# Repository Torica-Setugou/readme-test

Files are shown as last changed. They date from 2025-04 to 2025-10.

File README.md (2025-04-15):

# 接合班 引き継ぎ資料 班長業務編
## 目次
- スケジュール管理
- 予算
- 精度管理
- 班員管理
- 多方面との情報共有

## スケジュール管理
- 各班の年間スケジュールを立てるのは班長の最初の仕事である。これは、執行代が始まる前に済ませておくのが理想である。自分の代の設計思想,各班における新規性を取り入れる部分などが決定した瞬間から動き出すことが重要。代々、全体のスケジュールは執行代になって初めの役持ち会議ですり合わせるのが恒例になっているため、それまでに他班長,設計と新規タスクやある程度のスケジュール感を伝えあっておくとスムーズに執行代の製作を始められるからおすすめ。
- 接合班は、11月から本番機製作が始める。そのため、試作期間は8~10月の3か月のみである。その間で実現できる新規タスクなのかを判断してから、新規性を取り入れた年間予定を作ろう。じゃないと苦しむのはあなたたちです。この時、他班で取り入れる新規タスクが接合班に干渉する可能性まで考える必要があるので要注意。全部ひっくるめて製作可能なスケジュールを作るのだ！
- 年間予定で満足してはいけないよ。本番機製作からは特に、最低でも週ごとの予定はこまめに考えなければならない。例えば、
  - 11~12月(桁試験準備)のスケジュールは、9月末に週単位で作った。
    →桁がいつ届くのか、やすりに何日かかるのか…
  - 1~3月のスケジュールは桁試験直後の役持ち会議までに作った
    1月はテストでスケジュール考える暇ないよ
### スケジュール作成のコツ
- デッドラインを定める　ex)桁試験,全組,荷重試験…
- マージンを1週間位とる
- 作業のフローチャートを作り、各作業の所要日数から逆算していく
- 着手の日程を定める
### 進捗確認
以外に忘れがちなのは、実際に作業が始まってからの進捗確認。
今年は、インスタで流れてきた進捗管理スプシを見よう見まねで作ってみた。これがなかなか分かりやすく、視覚的に作業の遅延状況や順調さを認識できるのでおすすめ。
以下に、配布用のエクセルシートを置いておくので、使いたかったらご自由にどうぞ。



[配布用_タスク進捗カレンダー.xlsx](https://github.com/user-attachments/files/19748247/_.xlsx)

## 予算管理
- 各班の年間予算を決めるのは班長の業務である。予算を感がるにあたって、年間スケジュールを立てておく必要がある。そのうえで、前年の予算折衝スプシを分析して、必要なお金を算出する。(消耗品を忘れがちだから気を付けて)
- 25代の予算は105万。5万くらい余裕をもって申請しているから、足りないってならないように頑張っています。
- スケジュールと同様、現状確認も怠らないようにしています。こっちも、エクセルシートで作ったグラフに月末に使った金額を打ち込んで視覚的に残高を確認できるようにしました。これを作るには、月別の支出を立てないといけないので、なかなかな労力を必要とします。



## 精度管理
- 班に一人はOKかNOを判断できる人がいないとまずい。班長の役割じゃなくてもいいけど、副班長なり、何らかの役職を持たせておいた方が立ち回りやすくなるかな。というのは年末までの考え。最近は、役を持たなくても、各作業で、「この作業はこの人に聞けば大丈夫！」という人が1人ずついればいいかなと思えてきた。
- 実際、バンドソウを使う作業とか垂直に関してはすみかに任せっきりだし、すみかは役持ちじゃないけど不便を感じたことはない。逆に、役持ちになると視野が狭くなっちゃうから、役を持ってない人の方が全体を俯瞰できていたりする。こういう人は他の班にも存在していて、分かりやすいのはコクピの響互だね。この二人は特にその最たる例だと思う。本当に助かっている。役持ちじゃなく、精度管理できる様なひとに、会議内容を班長,副班長から共有すれば十分事足りる。

## 班員管理
- 自分の代と後輩について、何人いて、どれくらいのスキルをそれぞれが持っているのかを把握することが班員管理といえる。これを怠ると、一定の人にだけ作業が集中したり、本番機が始まって作業できる人がいないっていう事件が発生したりする。各代をしっかりと分析する必要がある。
- バンドソウやボール盤の危機管理も班員管理にはいるのかな。機械に慣れてない人に初めから細かい成形を任せたりすると、怪我のもとになる。実際にヒヤリハットでも経験してれば分かりやすいんだろうけど、意外に細かい危険もあるよというのは伝えておこう。

## 多方面との情報共有
- これ、大事。接合班は特に、他班との連携が多いから尚更。T字-コクピ班、かんざし-翼班、垂直リンク機構-電装班といった具合に、接合が終わらないと他班の製作が着手できないっていうことが起こりうる。そうならないために、どの作業がいつ頃終わりそうか、干渉する部分がないかを話し合うことが必要である。
- また、設計との情報共有も重要で、お互いにやりたいこと、できること、できないことをすり合わせておくことが重要。運営については、借用が発生するときに連携が必要になるため、ここの情報交換も大切。

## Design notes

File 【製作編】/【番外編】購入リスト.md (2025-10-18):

# モノタロウ購入リスト
- ここに載っていなければ、"ロイヤルホームセンター南千住"か"Amazon"で探せば見つかる




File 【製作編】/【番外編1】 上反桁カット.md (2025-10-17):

# 上反桁カット

## 24代(Ray)の上反角
- 偏心かんざし(中子)を使用
- 端側の桁径を落として、根側の桁に斜めに差し込むタイプ
- 中子はDMM.makeで発注(両翼でたしか14万)
- エポパテ(24hエポ+エロジール増粘剤)で接着したが、ねじり担保が不十分だったため、偏心フランジを作成した




## 25代(竜海)の上反角
- いわゆる桁焼きを導入
- 上反角部で桁径を落とさないでよいため、設計的な剛性UP
- Rayでは既製品同士の接着だけでよかったが、竜海では桁カットが必要となった
- ちなみに、桁発注先のスリーホープでも斜めにカットはしてもらえるようだが、1カット8万と言われた
- 竜海は2段上反だったため、カット代だけで64万⇒部内で加工することでコストカット
- このカットがなかなか緊張感のいるもので、ちょっとでも左右翼で桁長さが変わるとたわみが変わる
- "ミスの許されない","高精度"の斜めカットを8本もやらなきゃいけないため、終始ガン萎えしながら切ってた

S__62791684

## 上反桁カットの手順
① まず、2分割する
- ここの精度はいらない
- 気楽に行こう

② 必ず、きれいな縁の方から長さを測って、"上反角部(斜め)"⇒"端部(まっすぐ)"の順でマスターを貼る
- まず、きれいな縁から図った上反角部までの長さを測定してマスターを貼る
- その長さから使用長さを差し引いた分を測定してマスターを貼る
- マスターは、マステで何か所か仮止めした後に、クリアテープで固定すると切りやすかった

③ "上反角部(斜め)"⇒"端部(まっすぐ)"の順で桁をカットする
- 上反角部はミスってもきれいな縁側にマスターをずらせばやり直せる
- 端部はミス許されないし、ミスると設計値に影響を与えるから最重要項目

スクリーンショット 2025-10-17 231427

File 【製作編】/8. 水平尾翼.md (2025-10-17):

# 8. 水平尾翼
7F49A58A-82DC-40C8-B008-F76D33B60D1D

## 8.1. 機構(Ray)
- 桁にエビネットを打ち込んで迎角調整版の回転中心とした。
クナイは水平桁スパンの中心ではなく、テール桁に添うようにずらして接着した。


## 8.2. 接着方法(Ray)
①レーザーを駆使して、垂直桁に対して水平桁が直交するように仮止めする。


②水平の中心のリブの罫書き線に合わせて迎角が0°になるように部品を本接着する。
- 24代のゴリゴリの人たちと一緒に数人で半日かけて頑張った。

## 8.3. 機構(竜海)
福田のなんちゃって機構学を基に機構は考えました。
Ｍ科2年後期で機構学を学べるそうなので、ちゃんと勉強したらもっといいものができるかもですね。


E331C7FF-E697-48C7-85B9-4641E61322DE

部品は、以下の5つ
- 水平マウント
- クナイ
- ジョイント部品
 - フランジ(耳)
 - 迎角調整マウント

エポ抜きで合計200gくらい
62B900CD-F821-49E6-81BC-57193AB1ED82

## 8.4. 水平マウントの作り方
①MDFで治具を作る。
- 桁を治具にすることで精度を担保
- 真空引きするときに歪まないよう、中にカネライトを詰める。
- ボルト穴部分にM6スペーサーを埋め込む
- 固定はクリテのみにして、脱型をラクに
36C7E25B-A5B1-4F54-9043-97BB3D0BC56D

②積層する
- 積層構成は「0-0-45-0-0-バルサ-0-0-45-0-0」
- 2mmバルサを含めて11層

③成形
- 干渉しないように製図する
- スペーサーを入れ込むこと検討したが、公差が大きいという理由でボツにした

## 8.5. 接着方法(竜海)
- 水平の接着における前提条件として以下の3つの要素があることを理解しておく。
- これらがドンピシャになるように接着することが重要
- 「ヨー」「ロール」「ピッチ(迎角)」


⓪垂直の内棒接着とテールの鬼目ナット埋め込みまで完成

①水平桁にクナイを接着

64F91B38-F99B-403E-9861-0FF9F3199E24

②マウントにM6長ボルトを通し、垂直内棒に対してロールを合わせる。
720C8004-FAAB-4B62-AF3D-765164BA68EE

③テールにマウントを接着
 - マステで目張りしてから
 - 接着は30エポ
 
④水平桁にフランジを通し、クナイ,フランジ,水平マウントにM6長ボルトを通す。

⑤水平桁のヨー,ロールを確認し、フランジの接着位置を決定
B31F3569-46E0-4050-AAA3-0F05BB76B13F
E951E330-76D0-4908-BC5C-53F4EC77F39A

⑥水平桁にフランジを接着
 - アルテコで仮止め
 - 本接着は30エポ

⑦クナイのフランジ部分をリューターで切り落とす

⑥水平翼製作(翼班)

⑦クナイ,ジョイント部品,迎角調整マウントを0degの穴で締結

⑧水平翼の迎角を0degに合わせて迎角調整マウントを接着

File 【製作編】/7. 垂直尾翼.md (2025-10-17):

# 7. 垂直
7F49A58A-82DC-40C8-B008-F76D33B60D1D
- 鳥科では代々、サーボを用いた平行リンク機構を用いている。
- Rayでは、内棒(CFRP)と垂直桁の間にベアリング(ころ軸受け)を入れてラダー操作の平滑化を図った
- 竜海では、ベアリングの代わりにPOM(ポリアセタール樹脂)の円筒を入れた軽量化,平滑化を図った

## 7.1. 接着方法(Ray)
①テールにマスターに沿ってリューターで穴を空ける

②テール桁内部に30エポを塗る

③中子を内棒が刺さる位置まで滑り込ませる

④内棒を刺して、レーザー出し



## 7.2. 機構(竜海)
- 機構は平行リンク機構を採用(去年までを踏襲)
- 今年はサーボと垂直桁間距離を抑えて小型,軽量化を図った
- また、25代ではロックナットやねじロック剤を導入
  - ニュートラルが安定しない欠点をカバーするため
  - 飛行時のゆるみを抑えるため
- 秋葉原の「スーパーラジコン」で購入
2004D83C-8483-4797-ADE8-88B31B46DB51

## 7.3. 中子(竜海)
- 垂直の中子設計は、班員(同期&後輩)に一任していた。(とはいえ、一緒に考えていたため全部理解してるのでご安心を)
- 必要な条件は、"グラスホフの定理"のみだが、平行リンク機構ではほぼ考えなくてよい
- 今年のテーマは"小型軽量化","サーボ取り外し可能"

### 小型軽量化
- 垂直-サーボ間距離を短縮
- ロッド部品をM6⇒M4に変更
- 補強材として適宜カネライトを使用

### サーボと取り外し可能
- サーボの4隅にあるタッピング用の穴を拡張して、M2の長ねじを使用した。
- 中子には高ナットを埋め込んだ



## 7.4. 接着方法(竜海)
### 中子接着

① 中子に電装ケーブルを通す

② T字と同様の方法で内棒の位置を決定,接着

③ 中子に桁内側に添うようなカネライト治具を30エポで接着
 - 接着面積は少ないが、十分の強度を担保
 - 何より桁に腕を突っ込まない分接着がラク

### フランジ接着

平行リンク機構では、サーボホーンとフランジで以下の条件を揃える必要がある
- 桁中心からボルトまでの距離
- 桁上面からの高さ

→MDFの治具を汲んで以上のパラメーターを揃えた。
S__53436423

### 実際に動く様子

https://github.com/user-attachments/assets/fe7d19f1-72d2-4a0c-af30-e99af3f56bf8

## 7.5. 本番フライトでの様子
### 垂直尾翼取り付けの流れ
① 夜間保持終了時刻にテールにサーボを搭載

② 機体運搬直前に垂直フランジにロッドエンドを締結(ロックナットで接合)

③ 機体運搬途中でサーボの通電チェック

④ ニュートラル合わせ(1回目):サーボホーンとテールの罫書きの垂直を差金で確認

⑤ ねじロック剤でサーボホーンを本締結

⑥ 桟橋で垂直桁接合(ロックナットで接合) ←当初の予定ではプラホ上の予定だったが読売から指示がでた

⑦ サーボ通電チェック：テールから基盤までのコネクタが外れていた

⑧ ニュートラル合わせ(1回目)：後縁を翼副班長とダブルチェック

⑨ ドーサルフィン固定

### プラホ上での挙動

① フライト直前に左旋回方向に少々ずれているのを後方指揮が確認
S__167411735

② 手で動かすと、サーボのガタ(しょうがない可動域)の中でニュートラルに直った
S__167411737

③ 走り出しの衝撃でまた左旋回方向にズレる
S__167411739

- どうやら、ラダーが定常状態に戻っていなかったらしい

- ただ、サーボ自体に存在するガタも存在するため、さらに高みを目指すなら工夫が必要
- サーボの軸とサーボホーンの固定に使われる円盤は歯車状の構造のかみ合わせであり、既製品である以上多少のゆとりをもって作られている
- このガタを考慮してガタの中心またはあえてガタの端がニュートラルになるように設定するのか、ガタがないような構造を考えるのか、、
- 25代ではしょうがないと割り切ったが、こだわる労力があるならぜひ改善してほしい

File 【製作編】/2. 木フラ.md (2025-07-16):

# 2. 木フラ
S__51159047

## 2.1. 作り方とポイント
①ホワイトウッド板材に分割方向と垂直方向に中心線を引き、その線に合わせて穴あけマスターを張る
- ０端,1根：38×184×360
- その他：38×140×360

②センターポンチで円の中心にしるしをつける

③“美女と野獣(自在錐)”で円形を切りぬく
- 大きいクランプ2つでガッチリ固定する
- 刃の固定は複数人で確認する

④Φ6mmの短いドリルで4つのボルト穴をあける

⑤Φ6mmの長いドリルで2つの側面ボルト穴を開ける
- 万力を小さいクランプで固定する
- 木材が台座にほぼ垂直に立っているか確認する

⑥バンドソーで縦長に半分に切る

[木フラ_ボール盤_工程別安全チェックリスト.pdf](https://github.com/user-attachments/files/19749276/_._.pdf)

## 2.2. 接着方法
① 木フラ接着部に養生テープを2周巻く。その隣に1週巻く。



② 分割した木フラを桁にぴったりと接するように桁接着面をやする
- ここが踏ん張りどころ

③ 木フラの中心線(下図緑線)を桁の罫書き線(下図赤線)に合わせて30エポで接着する
- 木フラの穴あけ精度が重要



④エポが硬化したら桁接合をしてドリルでボルト穴を拡張する
- ボルトがガタつかない程度まで

## 2.3. ドリルの先端形状について
- ドリルの先端形状には、"先三角"と"先ねじ"の2種類がある。
- これらの違いによって使用用途別で向き,不向きがあるので注意が必要。

### ①先三角
- 先端が三角形になっている一般的なタイプ
- このタイプはボール盤やインパクト等、幅広く用いることができる
- 使用時には、穴を空けたい材に対して垂直に力を加え続ける必要がある
- 逆に、上から力を加えなけらば、穴は進まない

### ②先ねじ
- 先端がねじのようになっている特殊タイプ
- このタイプは、インパクトには向いているが、ボール盤には不向きである
- インパクトでの使用時
  - 先端のねじ形状により、始めのきっかけの力さえ加えれば、自身の推進力により穴を掘り進めてくれる。
  - 先三角のように力を加え続けなくても穴が開くため便利
- ボール盤での使用時
  - 始めのきっかけを与えると、ねじ形状の推進力で材が持ち上げられる。
  - クランプが不十分であったり、1点指示であったりすると材が浮き上がり、ボール盤の回転に追従して暴れてしまうため危険。
  - ただし、しっかりと2点止めでクランプ固定していれば、勝手にドリルが下に掘り進められていくだけで、あまり危険ではない。
  - 木フラで使う"美女と野獣"のうち、去年新たに買ったものは先ねじであるため、注意してください。

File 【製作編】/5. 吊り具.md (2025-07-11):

# 5. 吊り具
6A44E5E5-74C8-4AA1-B082-F8FC85E9DCC1

- 吊り具は、コクピフレームとT字をつなぐ部品です。
- でも、実はあんまり強度がしっかりしてなくても大丈夫なんです。
- なぜなら、フレームとT字の締結強度を受け持っているのはホースバンドだから。
- このことに気づいて、24代の本番機以降は積層枚数が11枚→7枚に減らしました。
- 他チーム(MaPPLとか)だと吊り具の上側がただのゴム板でホースバンドの間に緩衝材として挟んでるだけだったりする。
- ただし、吊り具の下側はフレームの高さを決めるために必要なので、精度とある程度の強度が欲しいところ。
- どっかの代で、やっぱり怖くね？ってなったら11枚に戻してください。
- ちなみに、積層構成は0°だけです。

## 5.1. 作り方とポイント(澪以前)
①下図赤線部の治具を作り、積層する。


C63A4170-E80B-44E7-A143-39A828A9E806

②成形する。

③下図青線部をスタイロで切り出す。



④アルミ角柱と積層物をブラインドリベットで締結する。

⑤積層物に③のスタイロ部品を接着する。

## 5.2. 作り方とポイント(Ray,竜海)
- 一言でいえば、新方式では、桁を治具として使った。
- なぜそうしたかというと、旧方式では赤線部治具の誤差と緩衝材部品の誤差が相まって積層物にスタイロがハマりにくかったから。
- 緩衝材部品はRayまではスタイロ,竜海ではカネライト
  - 特に理由はない

①下図のようなコの字の治具を作る。



②桁を①の治具に罫書き線に合わせて乗せ、反対側から青線部の緩衝材部品を乗せる。
S__51159048

③緩衝材部品,コの字治具,桁をまとめてクリアテープで保護し、積層する。



④成形し、ブラインドリベットでアルミ角柱と締結する。

⑤積層に使った緩衝材部品を接着する。
S__51257350

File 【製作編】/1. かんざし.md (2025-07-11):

# 1. かんざし
9D03ED82-0A8D-49DA-AA37-B976888E7A47

## 1.0. 概要
- 径差を埋める役割を担っている
  - 端側に行くにつれ、桁の直径が段階的に小さくなる
  - 太い桁に細い桁を挿して接合する

- 鳥科では、桧角材を用いた「木かんざし」を採用
  - プロペラ機のチームでは、ウレタンを充填した表面をカーボンで積層した「ウレタンかんざし」が多い
  - 径差が大きい部分では有効的だが、鳥科の径差ではあまり効果が感じられず、導入しなかった

- 24代機では、上反角を「偏心かんざし(上反角中子)」を外注しで作っていた。
  - 逆に言うと、かんざしが新円に作れていなければ思わぬ上反ができてしまう。

## 1.1. 作り方とポイント
①差し込み長さを養生テープでマークする
- ここを甘く見ていると、たわみの左右差が発生する

② 角材を均等に接着する
- 表面にエポが付着しないように頑張ると後でラク

③ やする
- 偏心していないかのチェックはこまめにやろう

④ GFを巻く
- 積層後GF厚みは1層:0.3mm,2層:0.4mm
- おそらくそれ以上は+1層毎に+0.1mm)

⑤ スズランで均等に圧着する
- しわが無いように注意する
- シュリンクテープでもいいかもね

⑥ 24h待つ

⑦ やする
- 微小なガラス粉末が舞うため、マスクをすることを推奨する

⑧ 粒度の高い紙やすりでやすって仕上げ
- 桁内面との接触を滑らかにする

- 桁径が太い桁は大体、やすりだけで2,3日かかる。
- 細い桁でも1,2日は想定していた

⑨ 膨張したかんざしのやすり直し
- Rayの時は、梅雨が短く湿気も少なかったため、あまり膨張しなかった
- 竜海の時は、5月末から6月頭にかけて雨が続き、第１回全組では組み上げ時にやすり直しが6か所程発生した。
  - 対策として、ドラッグストアで売っている除湿剤を翼の足元と桁に巻き付けたが、大した効果は得られなかった
  
## 1.2. 角材計算
かんざし角材の計算は、添付のExcelシートをうまく活用してほしい。
誰が見ても使えるように分かりやすくしたつもりだが、かんざしへの理解が十分でないと難しい部分があるかもしれない。
このシートでは、生協で売っている角材の寸法を基に長さ900mmとして計算しているのでご注意を。



[竜海_かんざし計算.xlsx](https://github.com/user-attachments/files/19748230/_.xlsx)

## 1.3. GFについて
かんざしにGFを巻くようになったのは24代から。正確に言うと、何代か前にもGFを巻いていたらしいので、復活させたというべきか。GFが担っている役割はいくつかある。

①やすり量の削減
- 売られている角材の寸法は1mm刻みである。
- そのため、例えば厚み3.2mmのかんざしを木材だけで作ろうとすると、4mmの角材を0.8mmやすらなけらばならない。
- 太い径のかんざしだと、0.1mmやするのに約1時間かかるため、途方もない時間を消費する。
- ここで、GFの厚みは約0.2mmであるため、これを考慮すると3mm角材+GF1plyでほとんどやすらずに済むということだ。
素晴らしいね。
- やする量が多ければ多いほど、かんざしが偏心するリスクが高まるため、GFを導入した恩恵は大分感じている。

②かんざし膨張の抑制
- かんざしが木材だけだった場合、湿気などを吸って外径が大きくなることがしょっちゅうある。
  そうなると、全組・TF前に翼が完成した状態の桁でかんざしのやすり直しが必要になるのでダルイことに。
- さらにダルいパターンは、鳥コン当日のフライト後。
  着水時に水を吸ってかんざしが膨張すると、解体場で桁が抜けないとかいう事故が起こる。
- 実際、23代「澪」のフライト後は、桁が抜けず、湖岸でリューターを使って切り落として翼を持ち帰った。
- 24代「Ray」の解体フローを作った際は、かんざしが抜けなかった場合のフローを以下のように作成した。



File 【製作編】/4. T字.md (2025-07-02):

# 4. T字
B7AF8E5F-0997-48B4-A707-CFBD6EC47BBF

## 4.0. 概要
- 機体の中心となるため、接合班の製作物の中で最も剛性が必要となる部品である。
- T字製作では、コクピ班のカウルや電装班のピトー管との干渉が生まれるため、連携が必要である。

## 4.1. 作り方とポイント
①FusionでT字の胴体成形スプラインを生成する。
- Fusionは26班長が生成

②マスターに沿ってリューターで切る
- スプライン曲線(胴体と0番の接触部)
- 胴体の長さ揃え
  - 竜海では0番中心から1700mmでカットした
  - スプラインカット用でマージンを取って発注している
  - スプラインマスターに0番中心までの距離を測っておくと良い



③胴体の内径ぴったりの円形マスターをはめる

④胴体の内側にウレタンを充填する

⑤ウレタンを金属やすりで成形する

⑥フィレットを発泡ブロックから切り出し、やする



⑦胴体と0番をレーザー出しして接着

⑧フィレットを接着

⑨CFに切れ込みを入れる
- しっかり計算すればするほど積層がラク
- 計算方法はどこを基準とするかで絶妙に変わる
- 本番1回目では、桁中心,や側面罫書きからフィレットの角までの距離で計算
  - ちょっとずれてた
- 本番2回目では、フィレとの展開図を作って切れ込み位置を決定
  - 1回目よりきれいになった

- 1回目マスター


- 2回目マスター
S__53436422

⑩11層積層
- 積層構成
  - 0,0,45,45,0,45,0,45,45,0,0
- 5層目後と11層目後にエポを浸したカーボンロープで縛る
  - フィレットの角,CFの端を重点的に縛る



## 4.2. 25代での変更点
25代機で従来版と変更した点は、以下の2つ。

①積層スパンの縮小
- よりパイロットの体格にフィットするようにコクピフレームの横幅が縮小された。
- 従来通りの積層方法だと、積層幅が縮小されると桁とCFの接地面積が小さくなってしまう。

  →縮小された積層スパンの中で桁とCFの接地面積を大きくするためにフィレットを小さくした。

②フィレットをウレタン→発泡に変更
- 従来のウレタン充填法だと、桁のスレスレまで金属やすりでやすらなきゃいけない
- 小さなフィレットを作るには、桁を傷つけるリスクがあり、別個でフィレットを作れたらアツい

## 4.3. メモ
- フィレット部分の積層について、従来のウレタンよりも発泡の方がCFの吸いつきが良く、積層中に剥がれないからよかった
- CFの切れ込みは、実測よりも計算で出した方がぴったりになった
- フィレット接着には目張りした方がよかった
- 床to壁の垂直ランキング
  - 4階奥(90°の場所有)＞＞3階奥＞312
- 重量
  - Ray3.4kg→竜海2.9kg

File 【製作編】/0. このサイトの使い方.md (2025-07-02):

# 接合班引き継ぎ資料 製作編
AA7BC7BE-5EB8-4786-BC3F-37AD3169151A
- 接合班での製作物を列挙していくと、意外に数が多い。全部を100%の詳しさで資料を残せたらいいが、できないかもしれないからわからなかったら福田まで連絡ください。
- 以降、本番機の製作時期が桁試験の前か後かで分けて時系列順に書いていく。製作順番も製作方法も25代を踏襲する必要はないので、あくまでも「25代はこうだったんだなぁ～」と思って下さい。

- 下図のマークをクリックすると、各ページの目次が見れます。
FAAC0D90-E147-45E0-81E8-263FD7A8A8FD

45BE8444-AF52-4E6C-B27D-78838296A761

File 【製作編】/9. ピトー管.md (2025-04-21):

# 9. ピトー管
接合班ではガワの部分を担当
## 9.1. Ray
- フランジの外径に合わせて作成したフランジにクロス1～2枚とロービングでCFRPパイプを積層
- パイプ先端に電装班がピトー管を装着
- 当日は養生テープで固定していた。
- ふたさっとからピトー管が飛び出るため、プランクに穴をあけていた。
S__51159045

## 9.2. 竜海
- チョウチンアンコウの形状に変更
- コクピフレームに固定具で装着し、カウル上面に穴を空ける。
- CFRPパイプで小さなT字を作って骨格とした。
- 接合班で担当したのは以下の赤枠部分
- 右図の固定具は30エポで仮接着した後、1個につきリベットで2か所締結した。



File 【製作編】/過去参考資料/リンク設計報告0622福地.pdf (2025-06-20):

2016.6.22
10 期コクピ班長 福地亮太

Gerbera リンク再設計概要

1. 設計概要
図 1 は，リンク摺動部外観．図 2 に詳細な構成を示す．

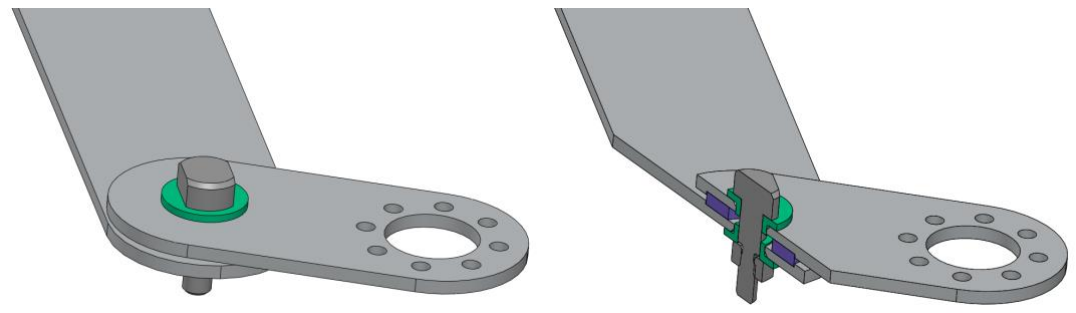
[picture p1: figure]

図 1 摺動部外観と切断面

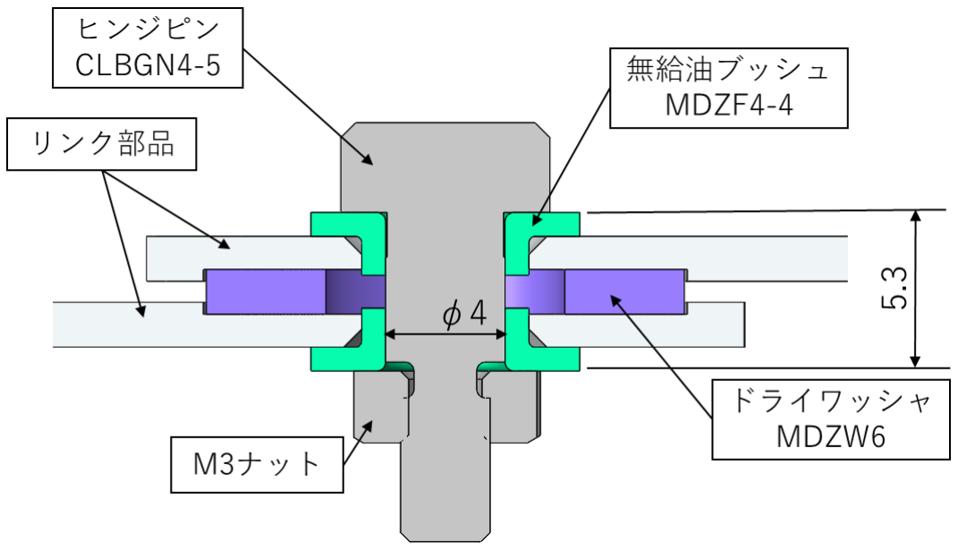
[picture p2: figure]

図 2 摺動部断面図

ドライワッシャをザグったリンクに埋め込むことで，ワッシャのカタツキを防ぐ．また， スペーサとボルトの役割を一括で担える部品に，ちょうどいい規格があったので，そちらも 紹介しておく．

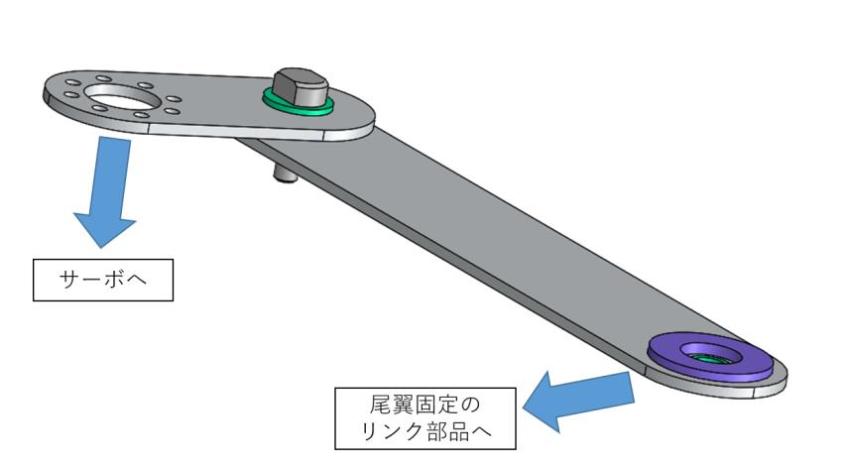
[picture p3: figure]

図 3 そりすぎて Soli

2. 用意してほしいもの
以下，ミスミの商品なので，アカウント作って購入して．

① 無給油ブッシュ

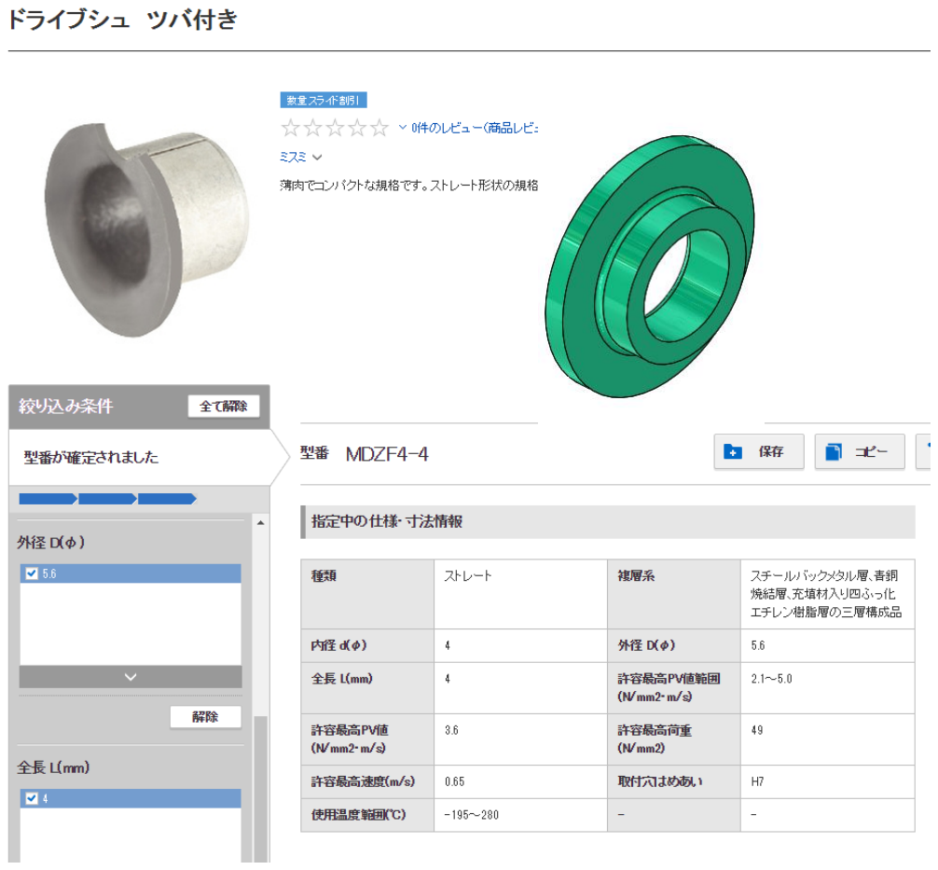
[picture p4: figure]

内径部とつばの部分，接触する部分の摩擦力を下げることができる．穴に圧入して使う． 最短でも長さ 4mm までしか無いので，買った後バンドソーなどで 1.8～2.2mm 程度に切っ てください．円筒形が崩れないような切り方は，工夫して．

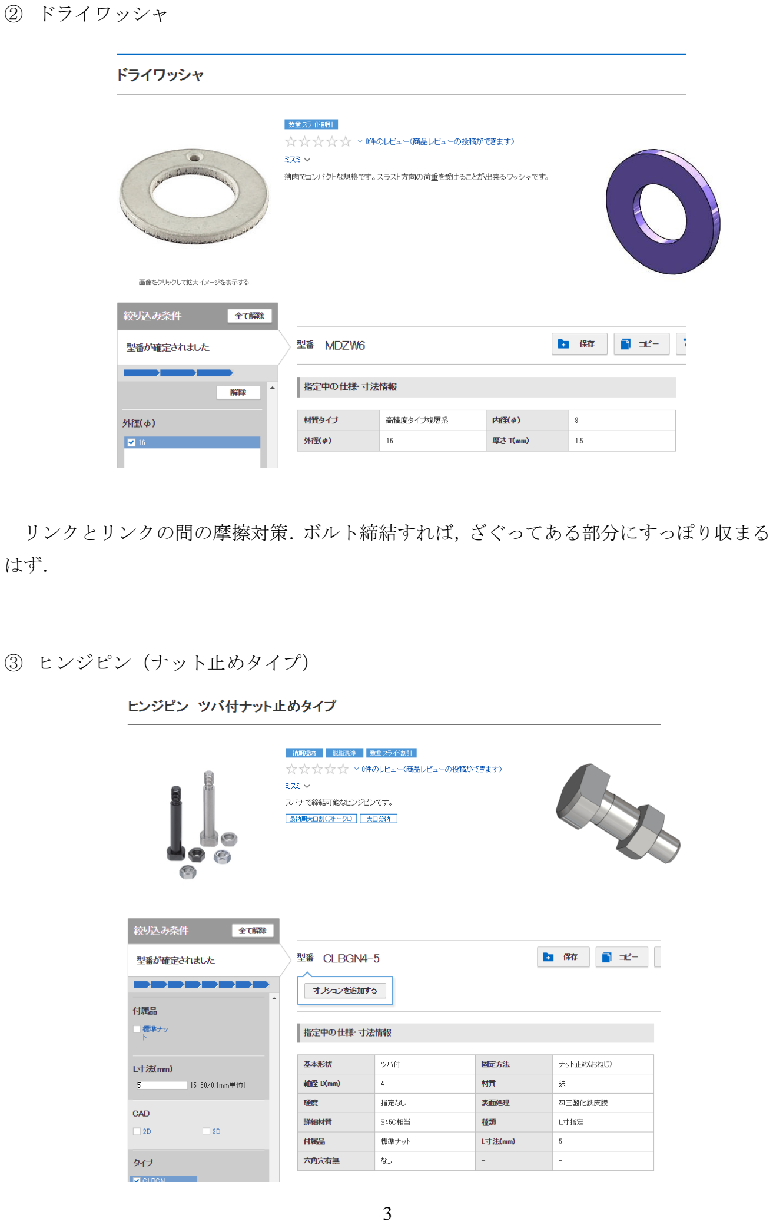
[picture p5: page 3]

② ドライワッシャ

リンクとリンクの間の摩擦対策．ボルト締結すれば，ざぐってある部分にすっぽり収まる はず．

③ ヒンジピン（ナット止めタイプ）

スパナで止められるタイプのピン．ねじ部が長すぎると思ったら，追加工できる．けど， 自分らで切れると思う．

ラダーだけなら
・無給油ブッシュ ×4
・ドライワッシャ ×2
・ヒンジピン ×2

エレベータもなら，上記の 2 倍用意してください．

3. 注意

★無給油ブッシュの外径はφ5.6．尾翼側の穴はすでにφ6 の穴が空いているので，無理やり エポかなんかで固定するか，それかつば無しのタイプは外径がφ6 の規格なので，そちらを 注文・加工して使用すること．

★ミスミは注文から，平日であれば 2，3 日で届きます．

★その他不明点，質問などは LINE か部室に福地を呼び出すか，研究棟 4 階の小林研究室ま で．

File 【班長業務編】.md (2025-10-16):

# 接合班 引き継ぎ資料 班長業務編
どうも、25代接合班長の福田です。
ここでは、私が班長として「何を心掛けていたか」に触れていきます。
班長業務は、外から見ても何をやっているのか分かりづらいと思うので資料を残すことにしました。

## 目次
1. スケジュール管理
2. 予算
3. 精度管理
4. 班員管理
5. 多方面との情報共有

## 1. スケジュール管理
- 各班の年間スケジュールを立てるのは班長の最初の仕事です。
   - 執行代が始まる前に済ませておいた。
   - 自分の代の設計思想,各班における新規性が決定した瞬間から動き出すことが重要。
- 代々、全体のスケジュールは執行代になって初めの役持ち会議ですり合わせるのが恒例になっている.
  - それまでに他班長,設計と新規タスクやある程度のスケジュール感を伝えあっておくとスムーズに執行代の製作を始められるのではなかろうか。
- 接合班は、11月から本番機製作が始める。そのため試作期間は短く、8~10月の3か月のみである。
  - その間で実現できる新規タスクなのかを判断してから、新規性を取り入れた年間予定を作った。
  - この時、他班で取り入れる新規タスクが接合班に干渉することもある。
  - 全部ひっくるめて製作可能なスケジュールを作るのが、なかなか大変だった。
- 年間予定ができても気は休まらない。本番機製作からは特に、最低でも週ごとの予定はこまめに考えなければならなかった。例えば、
  - 11~12月(桁試験準備)のスケジュールは、9月末に週単位で作った。
    →桁がいつ届くのか、やすりに何日かかるのか…
  - 1~3月のスケジュールは桁試験直後の役持ち会議までに作った
    1月はテストでスケジュール考える暇ないから前倒しして考えた
- ここまで私がスケジュール管理に躍起になっているのは、2度の桁試験をどちらもギリギリで乗り越えたから。
  - 1度目は製作ミス。2度目では情報共有不足。
  - このような土壇場でこそスケジュール管理が大事である。
  
### 1.1. スケジュール作成のコツ
①デッドラインを定める　ex)桁試験,全組,荷重試験…
   
②マージンを1週間位とる
   
③作業のフローチャートを作り、各作業の所要日数から逆算していく
   
④着手の日程を定める
   
### 1.2. 進捗確認
- 以外に忘れがちなのは、実際に作業が始まってからの進捗確認。
- 今年は、インスタで流れてきた進捗管理スプシを見よう見まねで作ってみた。
  これがなかなか分かりやすく、視覚的に作業の遅延状況や順調さを認識できるのでおすすめ。
- 以下に、配布用のエクセルシートを置いておくので、使いたかったらご自由にどうぞ。



[配布用_タスク進捗カレンダー.xlsx](https://github.com/user-attachments/files/19748247/_.xlsx)

## 2. 予算管理
- 各班の年間予算を決めるのは班長の役割です。予算を考えるにあたって、年間スケジュールを立てておく必要がある。
  - そのうえで、前年の予算折衝スプシを分析して、必要なお金を算出する。
  - 消耗品を忘れがちだから気を付けて
- 25代の予算は105万。削れるところは削りつつも、足りなくならないラインで申請した。
- スケジュールと同様、現状確認も怠らないようにしています。
  - こっちも、エクセルシートで作ったグラフに月末に使った金額を打ち込んで視覚的に残高を確認できるようにしました。
  - これを作るには、月別の支出を立てないといけないので、なかなかな労力を必要とします。



## 3. 精度管理
- 班に一人はOKかNOを判断できる人がいないとまずい。
  - 班長の役割じゃなくてもいいけど、副班長なり、何らかの役職を持たせておいた方が立ち回りやすくなるかな。**というのは年末までの考え。**
  - 最近は、役を持たなくても、各作業で、「この作業はこの人に聞けば大丈夫！」という人が1人ずついればいいかなと思えてきた。
- 実際、バンドソウを使う作業とか垂直に関してはS氏に任せっきりだし、S氏は役持ちじゃないけど不便を感じたことはない。
  - 逆に、役持ちになると視野が狭くなっちゃうから、役を持ってない人の方が全体を俯瞰できていたりする。
  - こういう人は他の班にも存在している。例えばコクピのO氏。
  - 役持ちじゃなくても精度管理できる様な人に、会議内容を班長,副班長から共有すれば十分事足りる。

## 4. 班員管理
- 自分の代と後輩について、何人いて、どれくらいのスキルをそれぞれが持っているのかを把握することが班員管理といえる。
  - これを怠ると、一定の人にだけ作業が集中したり、本番機が始まって作業できる人がいないっていう事件が発生したりする。
  - 自分の代の班員をしっかりと分析することはかなり心掛けていた。
- バンドソウやボール盤の危機管理も班員管理に入るのかな。
  - 機械に慣れてない人に初めから細かい成形を任せたりすると、怪我のもとになる。
  - 実際にヒヤリハットでも経験してれば分かりやすいんだろうけど、意外に細かい危険もあるよというのは伝えておこう。

## 5. 多方面との情報共有
- これ、大事。接合班は特に、他班との連携が多いから尚更。
  - T字-コクピ班、かんざし-翼班、垂直リンク機構-電装班などなど。
  - 接合が終わらないと他班の製作が着手できないっていうことが起こりうる。
  - そうならないために、どの作業がいつ頃終わりそうか、干渉する部分がないかを話し合うことが必要である。
- また、設計との情報共有も重要で、お互いにやりたいこと、できること、できないことをすり合わせておくことが重要。
- 運営については、借用が発生するときに連携が必要になるため、ここの情報交換も大切。

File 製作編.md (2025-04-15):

# 接合班引き継ぎ資料 製作編
- 接合班での製作物を列挙していくと、意外に数が多い。全部を100%の詳しさで資料を残せたらいいが、できないかもしれないからわからなかったら福田まで連絡ください。
- 以降、本番機の製作時期が桁試験の前か後かで分けて時系列順に書いていく。製作順番も製作方法も25代を踏襲する必要はないので、あくまでも「25代はこうだったんだなぁ～」と思って下さい。

## 目次
### 1. かんざし
### 2. 木フラ
### 3. フランジ
### 4. T字
### 5. 吊り具
### 6. テール
### 7. 垂直尾翼
### 8. 水平尾翼

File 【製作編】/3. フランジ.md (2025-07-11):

# 3. フランジ
66E2F516-BFC0-4830-8FE5-48B668F5C9BC

## 3.0. 概要
- フランジの役割は二つ

① 桁のすっぽ抜け防止

②桁のねじり担保

- かんざしがある程度キツく作られていれば、桁がすっぽ抜ける心配はほとんどない。
 
- ねじりを担保するにあたって、ボルトのせん断(荷重に耐えきれずボルトが破断しないか)や桁toフランジの接着力等の点を考慮する必要がある。
 
- 他チームでは、リアスパーや板状のフランジを用いたところも多いため、鳥科のようなフランジの形は意外と珍しかったりする 

## 3.1. フランジ積層
- 製作方法は特に資料いらないでしょう。代わりに、積層のコツを一言残しておく。
**「CFの言葉に耳を傾けろ」**
- 結局、これしかない。CFの繊維方向に対する生地の伸び方を捉えてあげれば、ヨレの少ない良いフランジができるでしょう。
- カネライト治具の寸法は、桁外径+0.5mmくらいでマスターを作ると桁に沿った良いフランジができます



## 3.2. フランジ成形
-  去年作った成形マスターの生成シートをそのまま利用した。去年から変更した数値はヘッド角度くらいかな。Rayでは120°だったのに対して、竜海では110°に変更した。この理由は、竜海の翼圧が大分小さく設計されており、120°だと翼面からフランジが飛び出す可能性があったからだ。
- ボルト穴の桁中心からの距離はほとんどRayを踏襲した。(RayはEclatを踏襲した。)ボルト位置を設定するにあたって、桁のねじりモーメントに対してボルトのせん断強度が耐えるかどうかを成田さん[24代設計主任]に去年計算してもらった。(今年はやまたくが計算してくれた)計算の結果、そこまで気にするほど荷重がかかるわけではないことが分かった。まあ、フランジやボルトが破壊される前に30エポの接着が剥がれるから、結局はちゃんと接着できてるかってことになると思う。




[竜海_フランジ成形マスター生成プログラム.xlsx](https://github.com/user-attachments/files/19749396/_.xlsx)

## 3.3. 接着方法
- 竜海は全区間、以下の方法で接着したが第一回全組でフランジがずれて接着されていることが発覚
- 穴の位置を桁に近づけた区間が4か所ある
- 改良が必要なので、頑張ってほしいところ
①フランジ接着箇所の翼を接合

②翼班の目で見て後縁がつながるように接合班が桁を回す
- 一番の沼
- 許容範囲が決まるまでは無限に時間が溶けていく

③マステで目張り

④対になるフランジをボルトで締結した状態で30エポを塗る

⑤前後縁の罫書き線付近に接着
- 翼面からはみ出していないか確認してもらう

⑥完全硬化する前に解体し、目張りを剥がす
- 解体時、フランジがずれないように十分注意する
- 30エポの効果度合いは感覚
- その日気温で硬化開始時間が変わるからね

## 3.4. ロービングについて
- Rayでは、30エポで接着した上から24hエポを浸したカーボンロープを巻いてさらなる補強を図った。
このロービングについて触れていく。
### ロービングの導入理由(Ray)
- Rayの前年機の澪では、下図のように接合部付近で桁折れが発生した。(再利用桁にクラックがあった説が有効)



- 機体が引き上げられた時には、破断部付近のフランジが完全に剥がれていた。
- ボルトは締結されたままだったため、過剰なトルクがかかった際にはボルトせん断よりも先に接着面の乖離が起こることを確認(そりゃ当たり前だが、実際に体感できる機会はあまりない)
- 桁toフランジの拘束力向上のためにロービングを導入



### メリット(個人的見解)
- ロービングが剥がれている箇所が何か所かあり、マイナスな意見が多いが、フランジの接着力向上はできていたと思う
- Rayがロービング導入初年度であるから、多少剥がれてしまうのはしゃあなくねというのが本音
- 30エポの圧着も兼ねてとCFロープを積層できたため効率的
### デメリット(個人的見解)
- 次世代で桁の再利用が困難になること
- 圧着中にフランジがずれるリスク有
- 基本、自分と龍司さん(24構造)でやっていた気がするが、慣れるまでは結構むずかしかった
### ロービング廃止理由(竜海)
- 一言でいうと、翼圧をだいぶ攻めた設計になったから
- ロービングをすると翼上面のふたさっとをやする必要が出そうで、早々にロービングの廃止が決定
- さらに、同様の理由でフランジのヘッド(接着面)角度も120°→110°に変更
- 結果、竜海では30エポのみで接着することになり、ロービングは廃止した。
### 総括
- ロープが剥離しないようにさえできれば、もっと肯定的な意見が増えたかなといった印象
- 桁の使いまわしや翼圧を気にしなくていいなら、CFクロスを積層してもいいなと思っていた

## 3.5. カーボンクロスの購入場所
- カーボンクロスは [**有限会社CAST**](https://shop.lab-cast.com/) という場所のWebサイトで **3K/平織 カーボンクロス** を購入している。
- 2mで1万円程度。
- ここでは、三菱,東レ,東邦の三社から在庫があるものを取り寄せてくれる。
- 各メーカーにより、多少クロスの硬さが変わったりするため、お気に入りのメーカーが見つかれば直接メーカーから買うのがいいかも。
- 知っている限り、23代～25代ではここから買っているが、対応がとにかく丁寧で発送も早いため不便を判じたことはない。
- ピールクロスもここで購入
  - 「ピールプライクロス」という名称になっているため注意
  - 厚手と薄手の2種類がある
  - 厚手は23,24代で使用
  - 薄手は24代の後半,25代で使用
  - 2種類とも買ったので試してみて

## 3.6. エポキシ樹脂の購入場所
- エポは [**FRP素材屋さん**](https://www.frpsozai.com/shopdetail/000000002128/) で **EPOLAM2031** を購入している。
- 主剤20kg,硬化剤6kgのセットで10万程度。
- 正直、あんまり使いやすくないので他のサイトがあったらそっちでいいかも。
- 余談だが、22代までは **Z-1** というエポを使っていたらしい
- このエポは人体に悪影響をもたらすことが判明して生産停止になったとか

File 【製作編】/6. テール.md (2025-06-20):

# 6. テール
## 6.0. 概要
- テールto胴体の締結には、空気抵抗となるためフランジを使用していない
- そのため、鬼目ナットという特殊な部品を使って直接ボルト締結をしている
- この部分の締結方法は今年でちょっと変えてみた

- テールには尾翼部品が取り付けられる
- 垂直尾翼を駆動させるためのサーボモーターを搭載するが、サーボは熱に弱いため鳥コン本番での熱対策が必要
- 熱対策としては、氷で耐えず保冷する方法と、桁を白く塗装する方法がある。
- 24,25代ではどちらも白く塗装して熱を遮断する作戦をとった

## 6.1. 作り方とポイント(Ray)
①T字とテールを接合する

②T字のロールを合わせて、垂直の後縁が垂直になるようにセッティングする

③胴体とテールにM6で共開けする
- ここ注意！
- 私はここでミスってT字をサイリすることになりました

④テールを解体し、鬼目の下穴を空ける

⑤テールかんざしに鬼目ナットを埋め込む

⑥同様に、合計3点留めになるように鬼目ナットを埋め込む

## 6.2. 作り方とポイント(竜海)
- テール桁の径が太くなったことにより、かんざしが肉薄に

　→かんざしに鬼目が収まらない

　　テールの内側に鬼目を埋めればいいじゃない
- そんな考えから生まれたのがこちらです。



①左図のような半月状の木材を切り出し、弧に対して垂直に鬼目ナットをつける。

②テール桁外部からボルトで締めながらエポで接着。
- ゴムワッシャーを挟んで締結

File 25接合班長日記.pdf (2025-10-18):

中田さん[24 翼班長]をマネて日記をつける。去年は途中で途絶えたから引退まで続けたい。

7.28 Sun

・24 年鳥コンが終わった。思うような記録は出なかったが、接合班としての安全確保の仕事は

十分こなせたはずだ。去年の桁折れから、安全性への意識が濃かったから、個人的には 1 年間

の努力が報われた気がした。

・解体はあれだけ会議を重ねたかいもあり、去年とは比べ物にならない程スムーズに終わっ

た。自分の仕事は全うできたので大いに満足だ。

・帰りの道中、加茂と二人で、俺らもう次期班長じゃなんかという話をして、マジで焦った。

執行代という実感はまだなく、翌日に控えた期末のことだけ考えるようにした。

8.5 Mon 接合班始動

・最後の期末科目が終わり、ついに接合班も始動できた。

・正直、26 代接合はやる気ありすぎてガチで怖い…テスト期間中も 404 に入り浸って作業を

求めている。当たり前のように部室にいるものだから、部室移動に向けて捨てる予定の古い桁

を使ってリューター練習をした。

・初めて使わせたが、俺が教えたとおりにやってくれて、慣れてきたころには安定して切れる

ようになってきた。(まあ、もうちょっとかなという感じはあるが、概ね大丈夫)リューターは

精度よりもまずは安全に使えるようになるのが重要。精度は今後勝手に上達するさ、きっと。

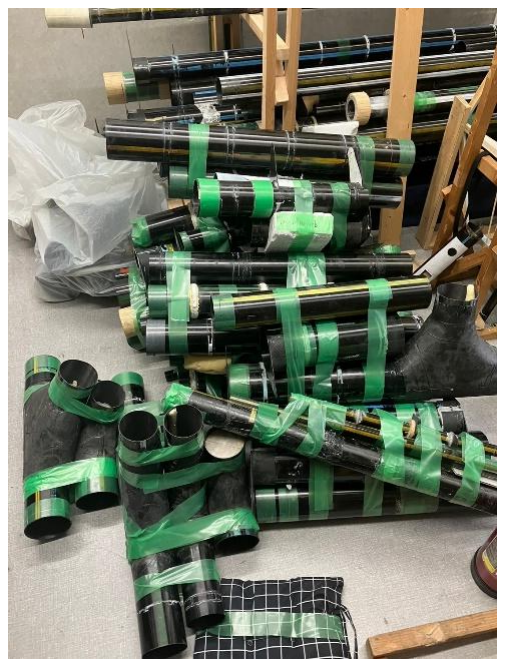
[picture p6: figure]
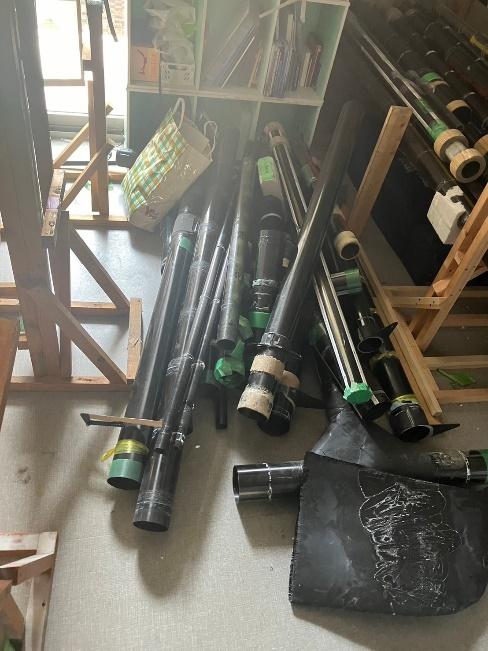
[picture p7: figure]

Before. | After

8.7 Wed 会議→作業→追いコン

・午前中は 25 役持ち会議があった。10 月に秋 TF をすることになった。接合班としては、新

たに作るものもないし、別にやってもいいや感はあった。ただ、9 月から乗り込み連をやる件

に関しては、いよいよ分身の術を習得しないとなと思った。個人的には、接合は誰が指揮すん

ねんといいたいところだが、こっちの事情でフラチの練習機会を減らすのは申し訳ないので、

言葉を飲み込んだ。

・今日に限った話ではないが、25 代役持ちは本っ当に会議が成り立たない。俺は 4 月の荷重試

験以降、会議では冷静に全体を見ようと心掛けている。バイアスはかかっているかもしれない

が、人の発言を遮った言葉や人の物量で押し切るのは会議とは言えないでしょ。

・自分の領分を理解すること、他の役持ちを信頼すること、頼み方の態度、言い方…ここらへ

んは最低限ちゃんとしたいね

・会議後は 26 代と一緒に古い T 字を 5 個くらい切った。これで桁切りは終了。ありがとう 26

代。うまく切れないとアドバイスを求めてきて貪欲に成長しようとする姿勢がまぶしかった。

8.8 Thu 桁,エポ捨て

・いわもっちゃんに来てもらって桁とエポを捨てた。よくわからん位古いエポも処分できた

・俺は 14 時から鳥コン反省会があったため、作業は 16 時からの桁捨てだけだったが、26 代

は当たり前のように部室に午前から居たらしい、若いって恐ろしい…

8.10 Sat オーキャン準備

・組み立ては順調に終わった。26 は積極的に接合をしてくれたので、こういう時にたくさん練

習させようといろいろ任せてやらせてみた。

・準備が終わったら、俺は 404 に眠る機材の動作確認と掃除をソロでやった。一方そのころ、

すみかの指示の下でフランジの治具つくりから積層までを 26 にやってもらった。

・俺はあまり直接見れなかったが、カッターと発泡カットは苦手だが、クリテ張りと積層はう

まいらしい、まあ、カッターも発泡カットもいかに回数をこなすかの作業だから、逆に最初に

センスが必要な積層とかが上手なのは今後が楽しみなところではある。

8.11 Sun オーキャン

・オーキャン終了後の解体で、26 が A 翼を落としてしまい、後縁が壊れてしまった。A-B 翼

解体の際、A 翼を馬を置いて B を抜くところを逆にしてしまって、A をうまく持てずに落とし

てしまったらしい。

・今回の事故は完全に自分の監督不行き届きが招いた結果であり、死ぬほど反省点がある。

①左右翼の解体が同時に行われていたことにより、俺がすべてを見切れていた訳ではなかった

②25 を一人つけていたし、全組で 26 にも何度もやらせていた作業だから大丈夫だとおもった

③飛び終わった機体とはいえ、緊張感持って解体するような呼びかけが不十分だった。

④監督する優先順位を間違えた。(よりによって乗り込み連で 9 月から使う A 翼で事故った)

⑤そもそも 26 接合に対して 25 接合の指揮者が少ない

⑥分身できれば

・これといった最適解はまだ見つかっていないが、今後の指揮系統について改善策をいくつか

考えた

①俺,大津で指揮を分担する→全体指揮は動くべきではない

②俺,すみかで指揮を分担する→指揮を分担する時点で俺が全体把握できていない

③並行作業はさせずに全員に順に作業を分配し、俺が一括管理→常に暇な人が一定数存在

④作業に関わらせる人数を減らして、俺が一括管理→関われない人はどうする

・なにが最適なのか、どうすればよかったのか、現状なにもわからずあたまを抱えるばかりで

ある。明日からは入校禁止で作業もないので、しっかり考えて乗り込み連開始までに体制を整

えよう。

9.13 Fri 後期開始

〇夏休みの総括

・夏休みは帰省した週もあり、すみかに大分負担をかけてしまった。

・1 対 10 弱で作業を進めるのはやはり大変らしく、NASA に助けを求めたこともあったとか

・休み中の作業としては、T 字ラック,かんざし試作 1 本,フランジ積層&成形 4 個という感じ

・カーボンクロスをなかなか購入できず、メインの作業が部室移動になってしまったのは後悔

・26 について分かったことといえば、カッター練習を極端に嫌うということ

・最後の方は山口,彪央あたりが自主的にカッター練習を始めてくれて嬉しかったなあ

〇今後について

・以外に試作しなきゃいけないことが多い

ピトー管,垂直,フランジ接着,T 字,などなど

・25 代 : 24 代 = 2 人 : n 人 といった状況で、試作に手を出す余裕がなさそうすぎて泣く

・すみかと相談して、接合の作業日は火,木,金にして、その曜日で 26 の教育、残りの月,水で

25 試作をしようかと方針を固めた

・桁試験までの 3 か月は、去年の桁試験直前くらい忙しいかも まじでやばい

・スケジュール組みがんばります…

9.27 Fri 9 月後半の総括

作業内容

〇荷重試験に向けてかんざし・フランジの製作

・26 代にかんざしを作ってもらったが、なかなかひどい有様

・角材を張っただけの時点でエポの厚みで偏心していた

・俺がきれいにやすって GF 巻いてもらったら、Gf がよれててぼっこぼこ

・去年まではそんなこと起こらなかったから予想外過ぎた

・原因はスズランの圧着が均等じゃなかったからだと予想

・できると過信して雑な作業されるのはなかなか心に来るね

・まだ本番機は任せられないかな(もうちょっとかな)

〇ピトー管の試作[福田]

・ピトー管の固定具を作ってみたら大成功

・まだ途中だけど、最難関ポイントは超えたから多分実現できる

・最近は教えてばかりで作業できてなかったから、やっぱり作業って最高だなとにちゃにちゃ

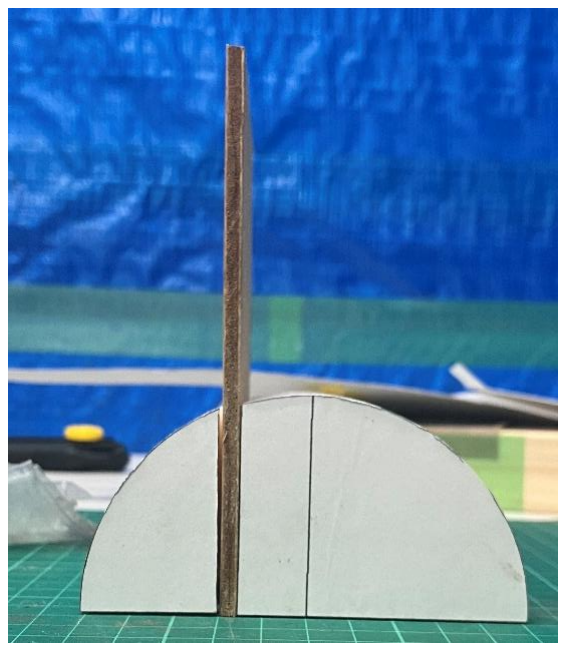
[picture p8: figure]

〇垂直中子試作[すみか]

・荷重試験まで忙しすぎることが分かり、早めに着手してくれた

・Ray の本番機を作っていたからより良いものを作ろうとしてくれていて本当に助かっている

・翼班の LC が直近だったから図面描く期間短かったけど、妥協しないでやってくれた

・いろいろ悩みポイントを共有してくれるとこっちも理解が深まって勉強になる

〇今後について① “TF”

・とりま TF の人員配置迷う

・全員を機体組み上げに配置するのはナンセンスだし、おそらく接合の大半は馬抑えになる

・現状、26 を左右 4 人ずつ配置してなさすみかに左右を監視してもらう予定(解体と同じ)

・↑桁接合,端側持ち,ボルト持ち,翼の真ん中保持の 4 人パーティ

〇今後について② “桁試験”

・桁届いてからのスケジュールがかつかつすぎる件

・2 段上反なのに桁届くのが去年と変わらないらしい(何なら去年より遅いと予想)

・上反桁に俺が施す加工が多すぎて一回くらいミスりそうで怖すぎる

・↑真っ二つカット 4 本 → 斜めカット 8 本 → 桁端マージン切り落とし 8 本((((；ﾟДﾟ))))

10.11 Fri 10 月上旬総括

〇桁試験日程について

・桁試験は延期になるんじゃないかなぁ

・11/7 日に出荷してくれるそうで、数本ならそれより先に出荷してくれるようになったみたい

・11 月 2 週目に届くってやつより半週~1 週間位は工期伸びたかな

・もうスケ表見たくなさ過ぎて開いてないからわからんが、カツカツスケジュールを遂行する

なら 1 週間位はマージンできるんじゃないかな

・それでも多分もっと遅くなるけどね

〇あれやそれや

・長谷部が辞める(これまでよく頑張った、俺も負担かけてた部分があるから心から謝りたい)

・多分俺も辞める(みんな、すまん。許してくれ)

11.30 Sat 11 月総括

〇11.8 桁が届く

・スリーホープ並びに運送会社さんありがとう

・分納はできなかったみたい

〇桁試験準備 ”木フラ”

・桁が届くまでに穴あけは完了できた。

ちゃんと穴あけを一緒にやって引き継げたのは虎央くらいだったと思う

・26 代が中間で忙しかったみたいで、あんまり経験させてあげられなかったけど、時期的にし

ょうがなかったと思う。許して。

・分割はすみかが頑張ってくれた。

11.29 時点で 0-1 以外の分割は終わっていた(ほんとにありがとう)

・廊下の使用が厳しくなったことでなにかと弊害を受けているが、身とシフトを削り何とか遅

延を最小限に抑えられている

12.8 Sun 12 月 1 週目総括

〇作業の現状

・かんざし：残るは 4 番かんざしのやすりのみ

・木フラ：穴あけ,分割までは全て完了

接着は素晴らしい進捗。

俺が立てた(立てざるを得なかった)キツキツのスケジュール通り進んでいる。皆ありがとう。

あと、自分もよく頑張った。

ここ 1.2 か月は心が休まる日は 1 日もなかった。

平日は毎日 10 時まで苦痛な作業。土日は生活の為にバイト。理大祭の裏でもずっと作業。

本気で辞めようと思ったが決断ができなかった日から 2 か月経ち、精神の安定は多少戻った

桁試験が終われば肩の荷が下りるのだろうか。心身ともに休めるのはいつだろうか。

〇26 代について

・ぼちぼち、設計が決まるようだ

・接合班長に興味があると言っているのは今のところ山田,彪央の 2 人

・接合班長は代々精神を病むポジションになりがちだから、彼らにはこうなってほしくないな

・「 せっかく人数がいるんだし、、」と、分業を勧めているが、実際どうするのかは彼ら次第。

・俺のようにはなってほしくないから、俺の 25 代としての反省点はこれから時間をかけて伝

えていきたい

〇伝えたいことメモ

・コミュニケーション(特に役持ち間,班員間)の重要性 違う場所の予定に苦しめられるよ

・やりたいこと/改善しなきゃいけないこと/できること/できないこと の区別

・先のことを考えることの重要性(予算,スケジュール,タスク数,班員の減少…)

12.19 Thu 桁試験準備完了

〇かんざし

・予定通りに終わった(怖い)

・やすり、GF 巻き共に一度も再履がなかったし、26 代がどんどん上手くなっていった

・試作の時との違いを考えた時に思いついたのは、一つ一つの作業にこだわりを持つようにな

ったことだと思った

〇木フラ接着

・せっかく精度よく桁穴を成形してくれたのに、ボルト穴の位置を俺が何か所かミスっていた

・マジで反省,萎えた

・今回は穴を空けなおすことで対処したが、精度は下がっているだろう

・やっぱり木フラじゃない方法を考案出来たら、それが一番だね

12.22 Sun 全桁組み

・人があまり集まらなかったため、馬抑えの人数を極限まで減らした。

・流れとしては、全体的にうまく進んだので安心

・ただ、0 番の縁にかんざしが当たったためか、周方向の最内層が剥離してしまった。

(剥離幅:約 2mm)

〇後日談

・剥離した部分に関しては、クイック 30 エポを薄く層間に塗ることで対処した。

・目張りをして、爪楊枝も使ってなるべく剥離部分全体に塗った。

12.24 Tsu 桁試験

〇桁接合

・いうことなし、完璧

〇桁リフト

・改良してよかった

・金額がかさむから、来年以降も同じ方法をとるかは会計との相談が必要だとおもう

・今年の方法だと、人,桁共に安全を担保できるからおすすめ

・デメリットとして、大量の人数を持ってかれることだけど、26 代の人数があるならいらない

心配だね

2.7 Fri 2 月 1 週目総括

〇積層台

・1 個目の途中までしか俺は関わらなかった

・2 個目からはとらおに任せて、26 代だけでやってもらうことにした。

・未だにカッターはやりたがらないけど、やっぱり皆で一つのものを作る作業は楽しいみたい

そりゃそうか

〇フランジ治具

・1 週間で 1/3 ずつ治具を作って、来週からフランジ積層に取り掛かる予定

・さて、集中力は続くのでしょうか、、

2.14 Fri 2 月 2 週目総括

〇フランジ

・去年の反省を踏まえて暖房は付けていたが、剥離祭りになっていた。

・おそらく、床に置いて真空引きしていたことによる床冷えが原因かと思われる。

・次の日から机の上において変えることにしたら、同じような剥離は起こらなかった

2.21 Fri 2 月 3 週目総括

〇フランジ

・円筒部分に盛り上がった剥離が起こりまくった

・原因として、フランジの隅にまで袋を密着させるのが難しいということで、試しに袋を大き

いものにしてみたことかなと考えている。

・正確に言うと、大きな袋が悪いのではなく、買ってきた袋が厚手で丈夫なものだったことが

原因と推理

・袋の生地が硬いが故に、真空引きの際に CF を巻き込んで剥離が起こったのではなかろうか

・フランジ積層の進捗は 1/2 程度だが、再履続きでメンタルがイカれてきたので、一旦フラン

ジは後回しに。来週から T 字の試作に着手する。

2.28 Fri 2 月 4 週目総括

〇T 字試作

・すみかの思い付きでフィレットを発泡にしてみることにした。

・コクピのカウルの端材を切り出してやすってみるとなかなかいい感じ。

・コクピから降りてきた積層可能領域が小さく、桁と CF の接地面積をより広くするために、

CF カットマスター(切れ込み)を CAD で作ることにした。

・ついでに、CF カットマスターは印刷した紙に切れ込みを入れてそれをなぞる方針にした

〇ピトー管試作

・T 字の裏で、ほぼ俺の個人タスクになっていたがピトー管の固定具と CFRP パイプの積層を

行った。

※T 字とピトー管を同時進行することになり、メンタルの許容量ギリギリではあったが、今週

も何とかやり切った。

3.14 Fri 3 月前半総括

〇ピトー管試作

・固定具の接着をした。

・接着方法はフレームを上下逆さに馬に置き、ホースバンドで固定した固定具に 30 エポを塗

ってピトー管のアルミパイプと接着した。

・アルミパイプと固定具の接着に 30 エポが相性が悪く、ちょっとの力で剥がれたため、リベ

ットを打つことにした。

・リベットを 2 本打ってみたが、最強すぎて、壊れるのが予想できないほどだった。

〇T 字試作

・胴体接着を 312 でやろうと思ったら床と壁の垂直があまりにもカス過ぎることが分かった。

・あきらめて、馬に平置きして接着できないか試してみたが、渋すぎた

・積層はうまくいった

・ウレタンよりも発泡の方が CF の吸いつきがよく、積層中に剥がれなくて去年より楽になり

そうだなぁ。といった印象

〇T 字本番

・今週は胴体のスプライン成形までやった。

・スプラインの生成はやまたくに Fusion で作ってもらった。

・メチャメチャ苦労しながら作ってくれたおかげで、かなりの精度で成形できた。(まじ感謝)

3.15 Sat 交流会

〇徳島大の操舵班の方と話して得られた情報

・板積層をする際は上から錘を乗せて圧着する(徳島大では、20ply で 5mm 厚)

・精度が必要な成形では、5mmMDF で LC したマスターを作って穴あけすると良い

・エポとアルテコはお湯をかけると剥がしやすくなる

・サーボが取り外し不可能なのはヤバイ

・自己潤滑性をもつ POM(ポリアセタール樹脂,別名:ジュラコン)をベアリング代わりに使用

・桁の内側に 1ply すると穴あけ時の最内層の剥離を抑えられる

3.28 Fri 3 月後半総括

〇T 字本番

・0 番-胴体接着は 4 階トイレ横のコンクリ打ちっぱなしゾーンで行った

・去年同様、正面,両側面からレーザー照射して垂直を担保した。

・去年よりも人手があり、レーザーの精度も高まったでしょう。知らんけど

・積層もうまくいき、3/20 に完遂された。

・後日談だが、竜海の本番コクピフレームをつけてみたら積雄幅にゆとりがあり、もっと積層

できたじゃ～ん。っていう話になったが気にしないでいいや

〇吊り具

・26 代に丸投げしたら、めっちゃいい精度のものを一発で成功させてくれた。

・去年は 2,3 回再履したから、すげえなぁの一言

〇剥離桁積層

・翼班が再履の為に桁掃除したら、彫刻刀で最外層をめくってしまったらしい

・その部分の補強として、ウェットカーボンで剥離部分を 1 週積層することになった。

・CF クロスを網目 1 つ単位で切り出して、一切ほつれないように積層した。

・気になる圧着はシュリンクテープ

・加温したかったが、24h エポの熱特性がよくわからなかったため、加温はしなかった。

・加温しなくても十分なテンションでシュリンクを巻けたため、その必要もなかった。

(この剥離に関しては、やっちまったのがどのタイミングかもわかっていないことが問題だと思

う。今後接するのが本番機である以上、一見大丈夫そうな小さなミスでも、ミスが起こった状

況をその場の責任者には共有されていなければならないはず。今回の件で分かったが、本番機

を触っているという自覚を持っていない人が多い良いんだろうなと思った。)

4.4 Fri 4 月 1 週目総括

〇フランジ

・積層は 4/2 をもって全て完了。成形はで 1/2 以上終わっている。

・このまま授業が終わるまでに成形までケリをつけたいところではある。

・成形が楽しいと言ってくれる 26 代もちらほら出てきており、来年の心配はしていない。

・俺がまたもやマスターを間違えて印刷していたことが判明したが、成形前に気づいてくれた

のでギリギリセーフ(マジで気づいた人ナイス)

4.6 Sun 垂直デー

・そろそろ垂直の引継ぎ(？)を始めないと。ということで開催された垂直講習会

・すみかによる講義→中子のカネライト切り出しの流れで開催

・最後には垂直フランジの接着方法の考案もみんなでできたので良い会だった

以降は軌道に乗ったため割愛

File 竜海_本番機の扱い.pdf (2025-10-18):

# 25,26代向け 本番機の取り扱いについて

### 4.25 MTG

目次

【前半】

### ・桁の扱い ・桁保持 ・工作機械の扱い

【後半】

### ・作業中のミス,本番機に傷つけた時の対応

目次

【前半】

### ・桁の扱い ・桁保持 ・工作機械の扱い

【後半】

### ・作業中のミス,本番機に傷つけた時の対応

## 桁の扱い

・アクセサリー等
例) 時計,ネックレス,指輪,ネイル,上着のファスナー,フード... おしゃれは自由ですが、、
原則作業中は外す
ムリなら絶対に桁に触れない,近づかない

・桁をたたかない
クラックの確認等、必要性がある時のみ例外

・工具,部品等を渡す際は、必ず桁の下から

## 桁の扱い[運搬時]

・部屋の出入りや曲がり角では、必ず声がけを行う
「桁出ます」「桁入ります」「桁通ります」

・桁は必ず、2人1組で両手で持ち、周辺の安全確認係を1人配置する

・桁の内側に手を入れて運ばない
理由① 両手で持てない→桁を落とす可能性がある
理由② 爪が桁の内側に傷をつける可能性がある

## 桁保持

・馬を踏んで、両手で押さえる

・馬の向きを必ず確認

・交代の際は必ず代役を見つけてから

・桁を下ろす時,上げる時は、指示があるまで桁に馬を添わせる 馬上部の角が機体にぶつかる可能性を排除

## 工作機械の扱い

〇バンドソウ,ベルサン,ボール盤,リューター,インパクト ・手袋をつけた状態,ひらひらした服装で回転機械を使用しない

例) ボール盤
・使用前に必ずテーブル,ドリルが固定されているか確認 ・必ずクランプを使用する

## 【前半のまとめ】

## 以上を25,26代全員が理解し、 27代に伝えなければ怪我人,サイリが増えるだけ

## あなたが思っているよりよっぽど危険で、 デリケートなモノを扱っています。

## 常に頭を働かせて、リスクヘッジしてください。

目次

【前半】

### ・桁の扱い ・桁保持 ・工作機械の扱い

【後半】

### ・作業中のミス,本番機に傷つけた時の対応

## 「作業中にミスしてしまった、、」

・機体にぶつかった
・作った部品の精度がいまいちだった
・部品を落とした
→①サイリしなきゃダメそう
②大丈夫そう
③自分では判断できない

いずれの場合でも班長陣への報告義務があります

## 「怒られるかも」

・ミスの責任を負わせることはない (分析,反省,改善はしてね) →勇気が出なければ、まずは同期に相談
一緒に怒られてくれる人を探す

・今からじゃサイリが間に合わないんじゃないか
→機体の破損を知らずに飛ばす方が危険
Pの命を預かっている自覚を持ってください

## 事例:桁の損傷

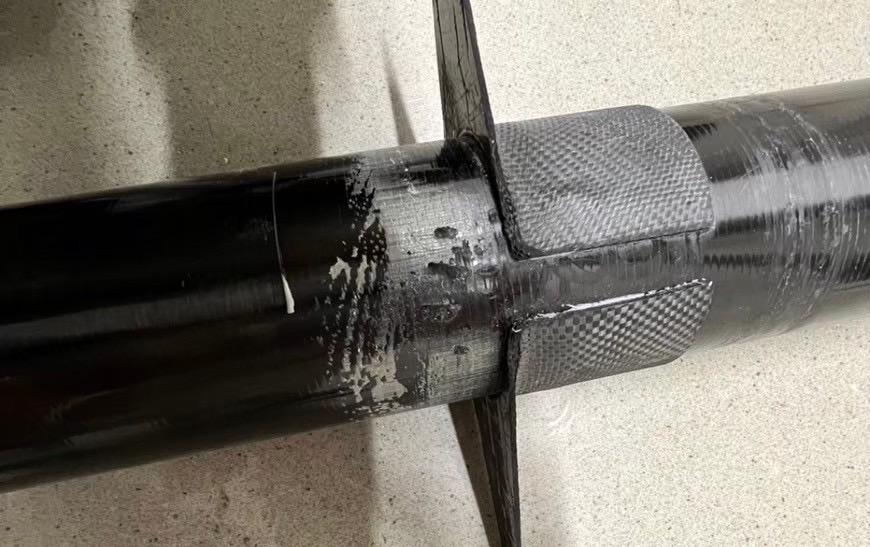
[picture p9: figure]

## 事例:フライト後

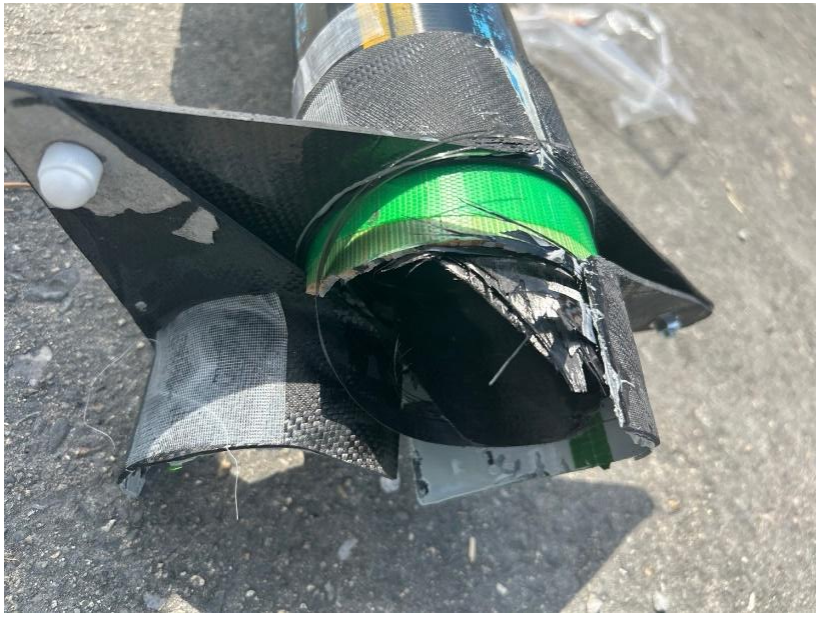
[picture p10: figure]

## 【後半のまとめ】

## ・モヤモヤしたまま飛ばすのは嫌じゃない？

## ・ミスを共有していれば、適切な処置がとれる

## ・25,26代の中で無理なら、 27代は25,26代には報告してくれない

【総括】

## 27代が入ってきたときの為に

## ミスの大小関係なく報告し合える 環境づくりをしてきましょう

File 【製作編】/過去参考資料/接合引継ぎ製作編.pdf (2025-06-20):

## 接合引継ぎ～作業編～

2017 年 8 月 8 日 | 園田 利希

## 1. 前置き

試験終わりに夜行バスで梅田に行く予定が、電光掲示板の誤表示で運休と勘違いして埼 玉に帰ることになるというかなりストレスが溜まる夏休みの幕開けとなりました。一応全 額返金ということになったので不幸中の幸いですね。余った時間で引継ぎ資料を作ってし まおうと思ったので作りました。作業に関してですが、特に重要な『上反角』と『尾翼周 り』について書きます。フランジとか T 字は交流会資料を見れば大体分かると思います。 ちなみに、これは作業編で、備品編と試作編も別であるのですが、紙媒体でしか存在しな いので所持者に問い合わせて下さい．．．

## 2. 作業状況

今年は 3 年 4 人（内 3 人神楽坂キャンパス）、2 年 6 人の 10 人体制でした。作業場に 10 人集まることはまず無く、集まったら集まったで、作業場の廊下の人口密度がヤバみで 熱気もヤバみだったのではないでしょうか。実はこれぐらいが適正人数だったと思いま す。一年間の作業内容は 1TB 鳥科垢の 2017 接合の作業報告.xlsx にまとめてあります。

## 3. 上反角

今年一番頭を抱えたことは、『上反角を付ける』ということでした。と言うのも、鳥科 歴史上でも上反角を付けた機体はよく壊れており、作成方法に関しても、詳しく書かれて いるのが 2015 年の Azure についてしか残っておらず、16 代の頃には試作をしておらず、 上反角の存在すら知らなかったからです。
そのため、17 代での試作期間では上反角の試作を 3 回しました。1,2 回目は Azure（つ まり津田沼）方式で製作して、これで本番機でもやろうとしたのですが、決めた上反角度 を付けるのが難しそうなので、3 回目に中子で作ってみました。土壇場でクリスマスに強 度試験して、なかなかの強度を誇っていたのでこっちの方式が採用された流れです。
- 中子式の製作過程
1. 製図を行う
まずは、中子の型を CAD で製図します。

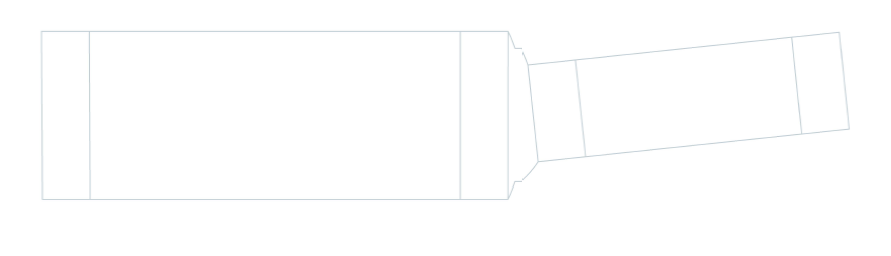
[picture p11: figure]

図 1 上反角

横の長さは、差し込む桁の内径×2.5 です。縦の長さは、カーボンプレートの厚さや GF の厚さを考慮する必要があります。上反中子.xlsx に計算式があるので参考にして下さい （図 2）。中央の桁径が変わる箇所の製図方法は接合ノートに書いたので見て下さい（割と 適当でもいいかも・・・）。真ん中の平らな部分は、試作でフランジを付けようとした名 残なので、無くていいと思います。

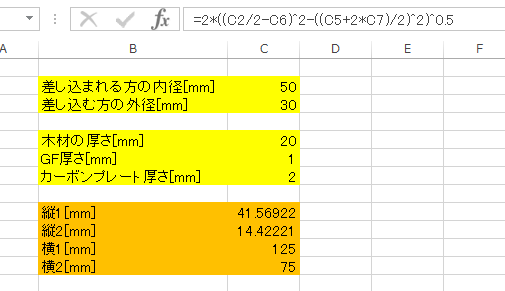
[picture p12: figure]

図 2 上反中子のエクセルシート

2. 木材を型に従って切る
1 で製図した物をボール紙にはっつけて切ります。それに両面テープを張って木材には っつけて、バンドソーで切断します。

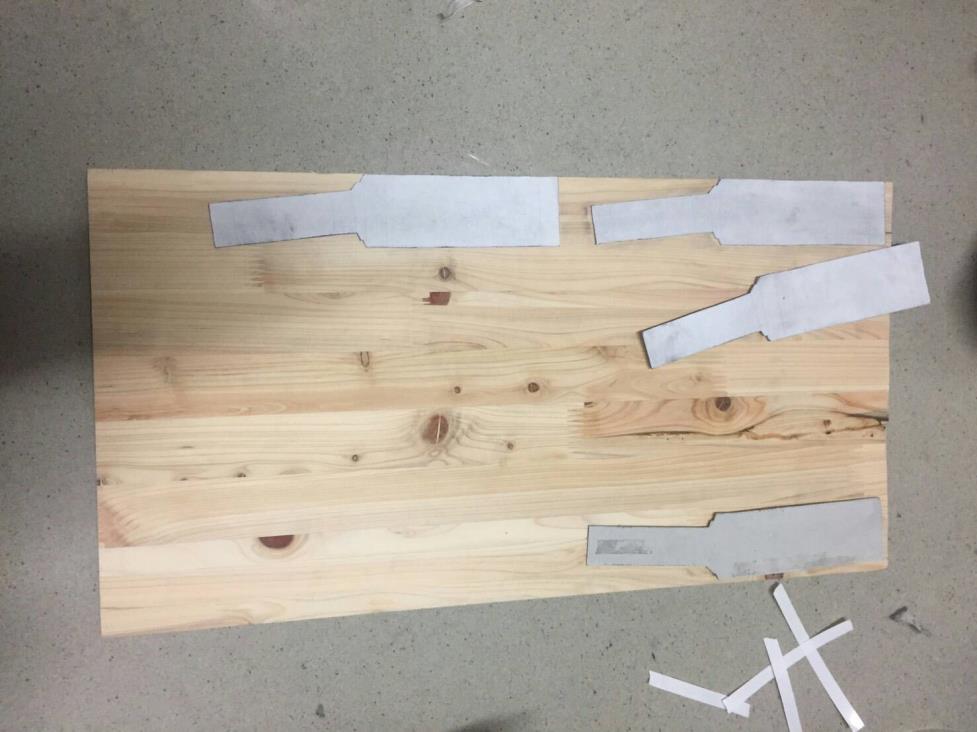
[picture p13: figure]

図 3 木材と型
桧をベースにしました。ここで厄介なのが、桧はそれなりに硬いので切断になかなかの時 間がかかります。めっさ疲れるのと桧のいいにおいが相殺されて無限に作業が出来ます。 刃が折れやすいので、刃の予備を多めに買っとくといいかもしれません。因みに、切った 時点で、側面に中央線を引いておくといいかもしれません。というのも、図 3 のように、 桁と接着する際に必要になってくるからです。

図 4 接着の様子、中心線にレーザーを当てている

3. カーボンプレートを型に従って切る
2 と同様、5 枚積層した CFRP を型に沿ってバンドソーで切断します。2 で切断した桧 にサンドするために作ります。

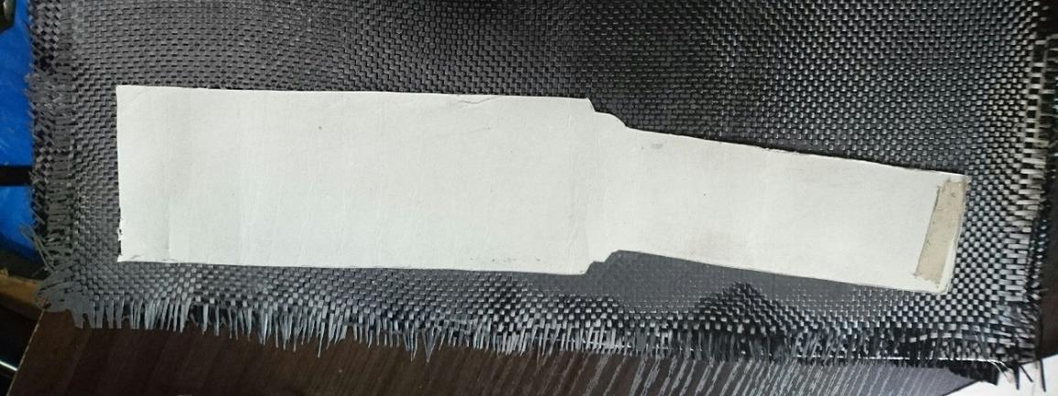
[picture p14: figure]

図 5 カーボンプレート切断
4. 木材とカーボンプレートを GF で巻いて真空圧着 流れとしては、①カーボンプレートに 50 エポ（増粘剤使用）を付けて、桧に接着。② GF に 50 エポを浸す。③GF で 2 周分包む。③キッチンペーパーで余分なエポを拭き取 る。④ピールクロスで覆う。⑤真空ポンプ 2 台で吸引。という感じです。ここで気をつけ るべきことは、吸引袋の作り方です。今回はゴミ袋に両面テープを張って作りましたが、 これがなかなか難しい。いっそのこと布団圧縮袋を使うといいかもしれません。

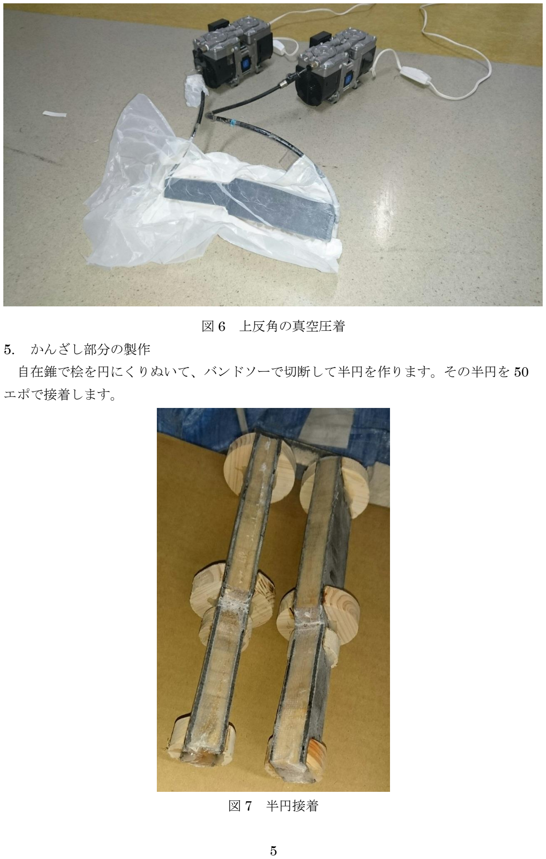
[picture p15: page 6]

図 6 上反角の真空圧着
5. かんざし部分の製作
自在錐で桧を円にくりぬいて、バンドソーで切断して半円を作ります。その半円を 50 エポで接着します。

図 7 半円接着

1 日置いて硬化したら、50 エポを浸した GF でかんざし全体を覆って、スズランテープで 縛ります（ピールクロスを忘れずに）。

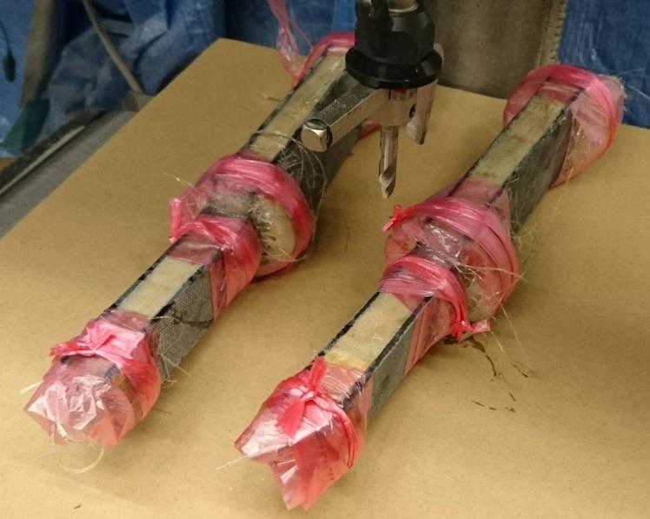
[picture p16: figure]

図 8 GF でかんざしを覆う

かんざしの部分なんですが、ここをしっかり作らないと前進角になったり後退角になった りします（実際にルミナスでは前進角が付いた）。しっかりとした半円を作るのは難し く、ここが最大の改善すべきポイントですね。

6. 小さい方の桁と合体
レーザーを使って桁を水平に置いて、桁と中子が水平になるように接着する・・・書く だけならば簡単なのですが、中子に角度が付いているせいで桁の罫書き線と中子の中央線 に、うまい感じに水平線が乗ってくれません。今年はたしか中子を付けてない方の桁端の 罫書き線に合わせていた気がします。

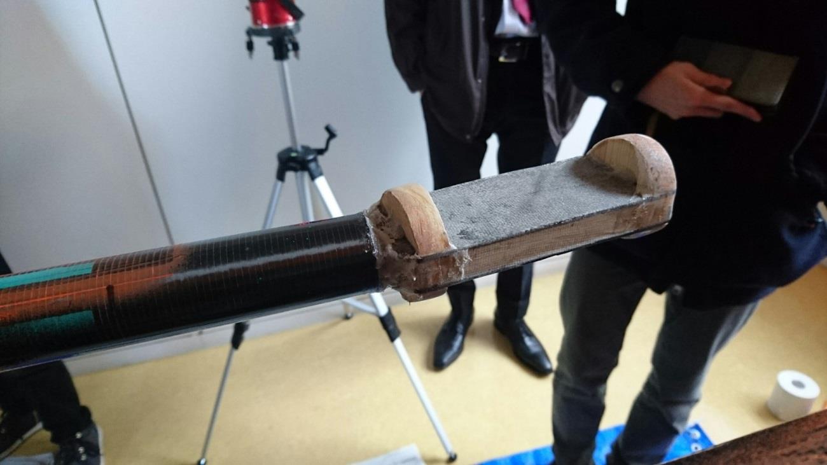
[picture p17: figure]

図 9 中子接着 1

7. 大きい方の桁と合体
馬 2 つと稼働馬 1 つを使います。馬 2 つで小さい方の桁を置き、稼働馬 1 つで大きい方 の桁を差し込んだ状態で置きます（図 10）。小さい方の桁の罫書き線に水平レーザーを当 てて、もう一つのレーザーで大きい方の桁の罫書き線に水平レーザーを当てて合わせまし た。適宜 90 度回転させて真正面から見ると、前進角、または後進角かどうか一目瞭然で す。また、接着後は追いエポするといいかもしれません。（図 11）

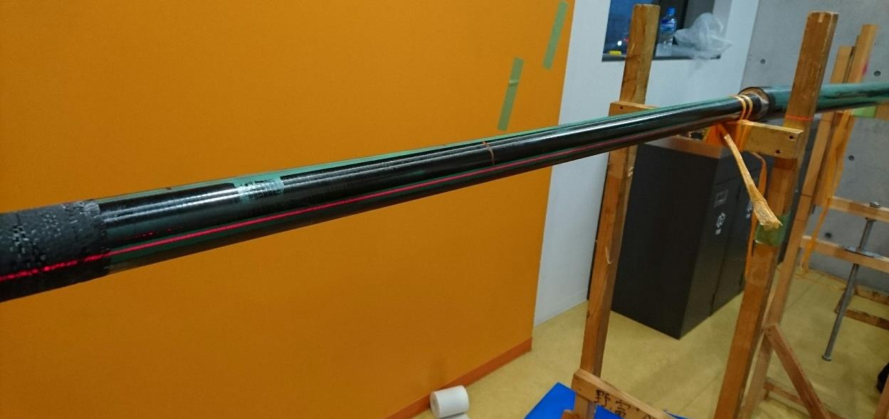
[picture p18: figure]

図 10 中子接着 2

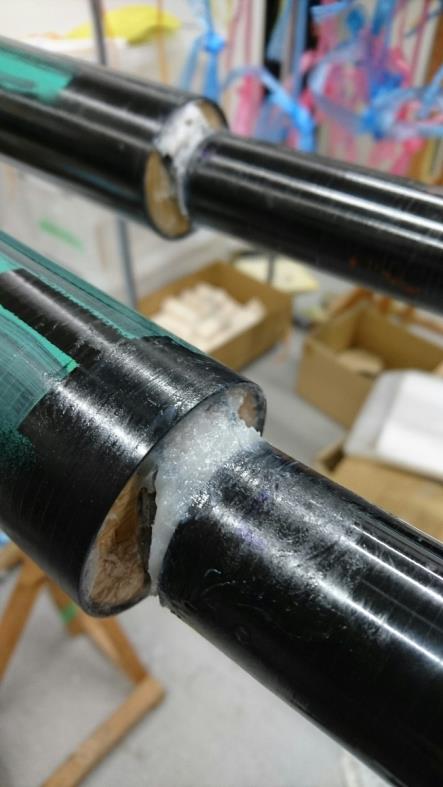
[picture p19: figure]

図 11 追いエポ

## 4. 尾翼マウント

今年も V 字マウントでしたので、制作方法は昨年とは大きく変わりません。ただし今年 はマウントのでっぱりが無いので簡単に作ることが出来ました。

- マウントの製作過程
1. 製図を行う
CAD で製図を行います。マウント接着の際に雌型もあった方が良いので、それも考慮し た方がよいです。
2. 型の製作
カネライト（スタイロ）を型に沿って切り出して、両面テープでくっつけます。マウン ト積層で使うのは雄型のみで、マウント接着に使うのが雌型です。
3. マウント積層
雄型の表面を軽くやすってクリテで保護して（図 12）、カーボンクロスを 7 枚積層しま す（図 13）。

図 12 マウント型（雄型）

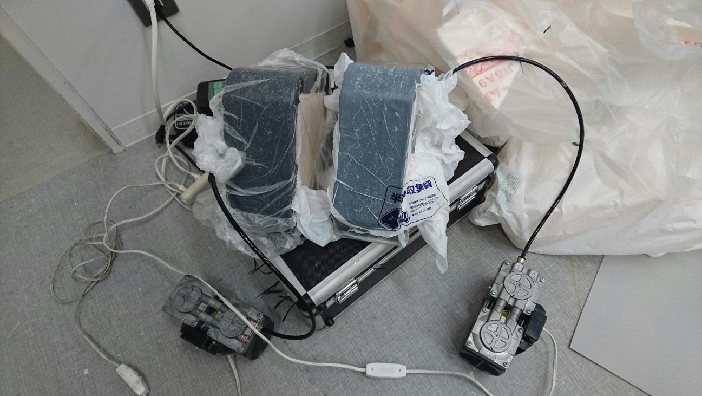
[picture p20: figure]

図 13 マウントの真空圧着
4. マウント整形
マウントを引き伸ばした物を製図して（図 14）、マウントに貼って、それに沿って整形 します。

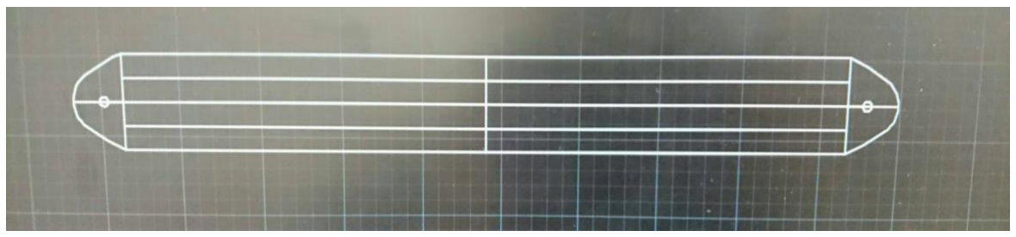
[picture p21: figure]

図 14 マウント整形用

- マウントの接着過程
1. マウント接着用の雄型を作成する
雄型の方は、積層したときにおちゃかになるので、新しく作る必要があります。同じ要 領で作成しますが、桁に乗っけられるような形にします。

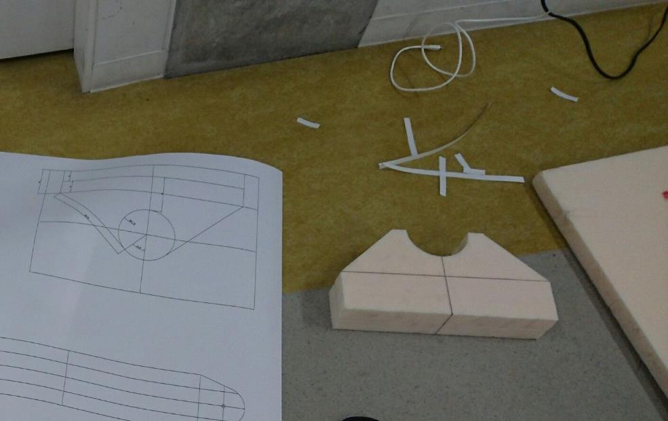
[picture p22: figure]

図 15 マウント接着用雄型

2. 桁に接着する
マウントに、桁が接する範囲に 50 エポを塗って、雄型と雌型でサンドして、スズラン テープで圧着します。このとき、桁を水平に置いて、レーザーを使って水平垂直につけま す。

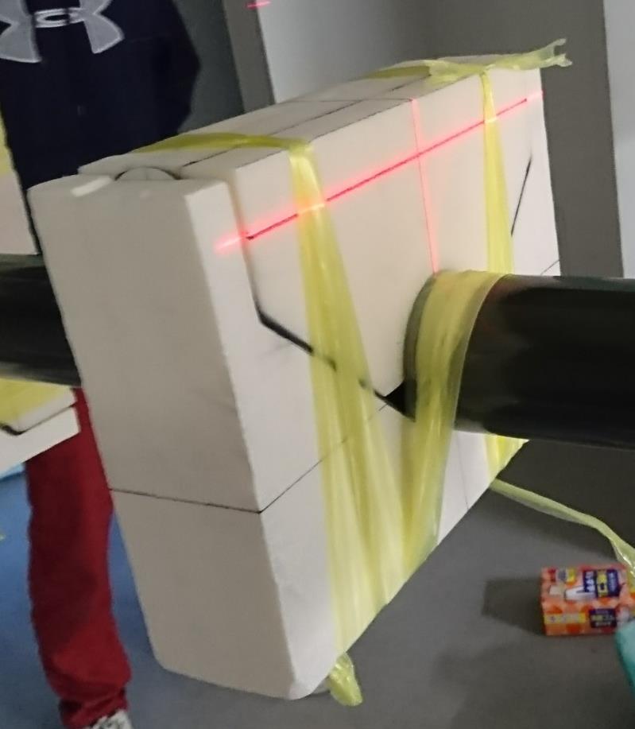
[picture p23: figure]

図 16 マウント接着

3. ウレタン充填
オーバーレイするためのパテ。流し込んで固まったら金属やすりでやすって整形しま す。

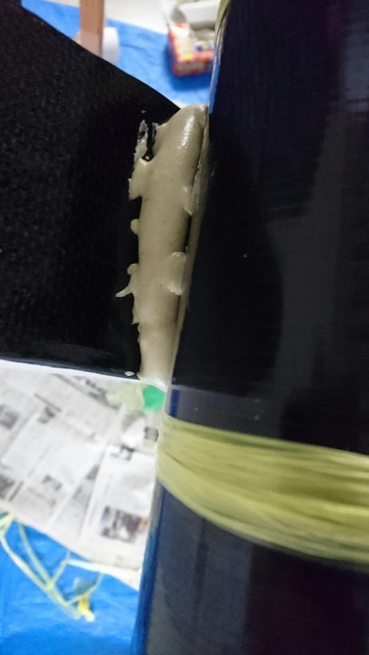
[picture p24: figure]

図 17 ウレタン充填

4. マウントオーバーレイ
オーバーレイ用のカーボンクロスを切り出します。上から被せる正方形×3（左右で× 2）、下から被せる箱を広げたような形の奴×5、ウレタンでパテ盛りした所を巻くベルト 状の奴×1（左右で×2）図 18 に形状を示します。


図 18 マウントオーバーレイ用カーボンクロスの形状

カーボンクロスを被せる順番としては、①上面（図 19）②下面（図 20）③ベルト（図 21）となります。

図 19 上面

図 20 下面

図 21 ベルト

ピールクロスは、上面と下面から被せます。養生テープでピールクロスを固定するといい です。


図 22 ピールクロスを乗せる

真空引き用のビニールで覆う必要があるのですが、あらかじめ真ん中に切れ込みを入れて マウントの片方に入れて両面テープで密封したらうまくいきました。

図 23 ビニールに切れ込みを入れる


図 24 マウントにビニールをくぐらせて両面テープを貼る

図 25 真空引きの様子

- 全ねじを通すための穴あけ過程
1. 片方の穴をあける
貼ってある紙の穴あけ位置に穴をあける。
2. もう一方の穴をあける
穴位置を決定するためにレーザーを用いる。このとき、雄型の型をマウントにはめてお く。開けた穴に水平、垂直レーザーを当ててマウントの角に印を付ける。


図 26 レーザーの配置

次に、水平に関して、角につけた印に横から水平レーザーを当てて、反対側の角に印を付 ける。また、反対の側面に関しても同じように行う。


図 27 水平方向の位置決定


垂直方向に関しては、桁を 90 度傾けて、垂直線を当てて反対側の角に印をつける。水平 垂直どちらとも印を付け終えたら、印に乗せるように水平垂直レーザーを当てて、交わった 点が穴をあける位置になります。

図 28 穴あけ位置確定

その後は実際に全ねじを通してみて水平垂直になっているか確認します。水平尾翼に水平 レーザー、垂直尾翼に垂直レーザーを当てて両方乗れば大丈夫です。

図 29 マウントの直交確認

## 5. 尾翼リンクパーツ

尾翼パーツの取り付け方法は去年とさほど変わらないはずなのに、ことごとくミスしま くって大惨事となったので、これは引き継がないとヤバみな感じがしました。50 エポで接 着したものもカッターでずたずたにすればひっぺ返せることにも気付けましたが、あまり よろしくないでしょう。
- 水平垂直桁に付けるリンクパーツの製作過程
1. リンクパーツの作成及び木のリング作成
リンクパーツはカーボンクロスを積層したものを整形、木のリングは自在錐で穴をあけ て完成。木材は軽さ重視で桐がよいと思います。
2. 木のリング接着
桁に通して 50 エポで接着する。このとき、垂直レーザーをリンクパーツに当てて、垂 直に付くようにする。スズランテープでうまい感じに圧着させる。


図 30 木のリング接着

このとき、スズランテープで縛ったら桁から取り外さないと桁にくっつく恐れがあるので 桁からとって硬化待ちします。

図 31 硬化待ち

- 垂直尾翼への取り付け過程
マウント幅とサーボモータの幅を考慮して取り付ける必要があるため、確実に取り付け るためにシャフトに印を付けて、その印を参考にして位置調整します。手順は構造設計の おきにきが書いた奴の通りです（図 32）。


図 32 おきにきが書いた垂直リンクパーツ取り付け方法

シャフトに印を付けるときは、マウント幅とサーボモータの幅が分かるように CAD で印 刷するといいと思います。


図 33 シャフトへの印付け

作業の様子を図 34 に示します。

図 34 垂直桁へのリンクパーツ取り付け

横から垂直レーザーをリンクパーツに当てて垂直についているか確認しましょう。その他 の確認事項は図 35 に示します。


図 35 おきにきが書いたパーツ取り付け時の注意事項

- 水平尾翼への取り付け過程
基本的には垂直桁の場合と変わりません。こちらの方は水平桁の中央を基準として取り 付けていく感じになります。中央リブが入ることを考慮して、あまり桁にエポをべちょべ ちょつけないように気をつけて下さい。

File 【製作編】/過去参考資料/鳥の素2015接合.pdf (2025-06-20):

# 2015 接合班作業報告


2015 年 8 月 8 日 | 山本健介

yama3394145@outlook.jp

## 1. はじめに

暑いですね、夏本番といった感じでしょうか。東京は 2015 年八月、観測史上初の八日連 続の猛暑日を記録したそうです。余談ですが東京においての気象観測の始まりは 1876 年に も遡るそうです。そんな糞暑い夏休み序盤の今日、私が発した言葉の九割くらいは「すみ ません鼻毛の方には触れないようお願いします」だったと思います。何を言っているかよ くわからないと思うので順を追って説明すると、さいたまスーパーアリーナで行われた子 供向けの科学イベントで私は巨大な鼻のモニュメント（中に入れる）の列の誘導担当であ ったのですが・・・その日、モニュメント内の天井に付いてる鼻毛に、子供がぶら下がり 鼻毛が抜け落ちるという事件が発生したんです、この珍事件のため私は親子の前で声を荒 げなければならなかったのです。スーパーアリーナから帰還した私は何故だか 2015 年 7 月 25 日以来初めてかもしれない穏やかな気持ちを迎えたので、2015 年度の接合班の製作をま とめこれを引き継ぎとし、明日の鳥科に捧げたいと思います。

## 2. はじまり

2015 年度の機体 Azure の製作は 2014 年の 9 月ごろにスタートを切りました。2014 年の シランが琵琶湖の空で華麗に舞ったその翌月くらいです。Azure の 2014 年のシランとの設 計上大きく異なる点はかなり多く存在すると思いますが中でも大幅変更になった上反角の 存在でしょう。上反角の存在意義に関しては一言でまとめるとロール方向の安定性の向上 という話だったと思います。詳しい解説に関しては 2015 年設計主任が資料なりに残してい るでしょう。鳥科には過去二回にわたってこの上反角が折れるという苦い思い出がありま した。そういった経緯もあり設計主任からは「とにかく壊れない上反角を作れ」という命 を受けました。
一番最近では 2012 年のシーガルは 258m という記録を残し、その際上反角は無事生還し ました。上反角の製作が決まってからはシーガルの資料を漁り、何も知らない私は製作方 法を見出そうとしたところ、どうやら内部の構造に NC ナイロンという素材を使っている ということは判明したのですが、ただこの NC ナイロンは鳥科の工作技術では加工するの は到底無理で工作室の人間にすべて依頼して作ってもらっていました。僕の中のつまらな いポリシーで「なるべく自分たちの手で」というものが存在しました。こういった人それ ぞれのつまらないポリシーや意地はものづくりをする上での人間関係などに悪い作用とし

て働くことも多いですが、力の源泉やモチベーションに十分なりうると思います。今回は 私自身のそれを尊重しました。だからといってシーガルの製作で使われたアイデアを没に するのではなく、そこから様々なノウハウを吸収し、新たな上反角の製作の糧としました。 ちょうどその頃の我々は奈良の平城京が唐の長安を模して建造されたように何か母体とな るベース、模するべき対象を必要としていました。その答えは他チームにありました。日 大津田沼さんの内部構造を基にすることに決めたのです。

## 3. 津田沼さんと 2015 鳥科の上反角

この業界では「差し込み式」と「中子式」の二つの方式が上反角構造の主流となっていま す。この両者の違いについては鳥科内の沢山の資料に載っているのでみておくと良いでし ょう。とりあえず 2015 年においては、「中子式」が却下になった理由としては、桁間を接 合するジョイントの形状が思ったより複雑であったというだけです。作れる見通しと時間 があればチャレンジしてみると面白いかもしれません。下の図（Fig.1）は津田沼さんから 頂いた内部構造ですが、これが今年採用した「差し込み式」です。（便宜的に今後の説明で は外側の径の大きい桁を外筒、内側の桁を内筒と表現します。）


Fig.1 津田沼上反角内部構造

津田沼式の素晴らしいところは、なんといってもシンプルな平面パーツのみで構成されて いることでしょう。複雑なパーツを使うほど誤差が積み重なり、再現性が低下します。も し両翼の上反角度に差が出ればまともな飛行はできないでしょう。両翼の角度差を極力尐 なくするというのが一番大事なポイントと言っても過言ではないでしょう。因みに、2015 の鳥科は津田沼さんのを尐し改良して、円盤を一枚増やし（計三枚に）台形状の板を上下 に四枚追加しました。Fig.2 を見てもらえば大体わかるかな、と。

4. 製作

上反角の細かい製作手順についてはあまり触れませんが、大まかに説明していきます。

- 積層板の作成


Fig.2 積層板セッツ

Fig.2 はレーザーを使って積層板を桁に五分エポで仮固定している絵です。この状態で 15 分程度は keep してなきゃなので手がぷるぷるにゃ。積層板セッツ？は置いといて、積層板 の創り方はというと「そんなの積層するにきまってんでしょうに」ち・ん・ち・んでお終 いになってしまって面白くないので積層する際に意外と忘れがちな注意すべき点を書いて

いきます。

1) フランジと異なり、積層板はその名の通り板なので基本的に平面形ですので、脱泡ロ ーラーを使えます。脱泡ローラーを使うと層と層をムラなく密着させることができます。 また、繊維にエポキシを浸透させることができるので、脱泡ローラーは非常に重宝でき るファッションアイテムです。使用後は有機溶剤（アセトンなど）でしっかり洗浄しま しょう。これを怠ると・・・タスク後の洗浄は欠かさずに。（みんな洗浄しやすいから いいよね、外界の刺激に慣れてないから痛くて無理、大人しくクリーム塗ってます よ・・・。）


Fig.3 恥ずかしがるシアンちゃん

2) 離型剤を使いましょう。平面板の積層は金属板でサンドして圧着しますが、金属板に 予め離型剤を塗っておきます。離型剤を使うと表面が綺麗になって精神衛生上に有効で す。中身が重要と言いますが、そんなもんは所詮言い訳に過ぎないのです。
3) なにか書こうと思ったけど忘れた。忘れがちな注意点であるから仕方なし。そういや 今日は 8/19 です。これを書き始めた 8/8 ぶりに pc に向かっております。最近はバイト とバイトとバイトって感じの生活です。他に何してるかって言ったら普段あまり本を読

まないのですが、「失われたときを求めて」という作品にはまっています。話の内容自 体は朝の NHK の連続テレビ小説のような主人公が劇的な人生をおくる、という趣旨の ものではなく、日々の日常の生活を作者のプルーストのフィルターを通して見てみると なんじゃこりゃって具合な内容です。（ただ文庫本 14 巻まであるので一年以上かかりそ う・・・）あっ一つ言い忘れてた、積層枚数は確か 11 枚でした。思い出しました。積 層板を作るときに大事な要素としてサンドするアルミ板の存在が挙げられます。このア ルミ板が凸凹になっていないかなどまずチェックしましょう。（僕はあまりきにしてな かった）その後、アルミ板の表面を水ヤスリで軽く磨いて、ブルーワックスを塗り乾燥 させて離型剤を塗るまですればもはや言うことはないでしょう。因みに僕はそんな面倒 なことしたことないです。

- 積層板セッツ？

最初に円盤を桁に対して五度にセットしなければなりません。（2015 の上反角は五度とい う前提のもとです）


Fig.4

Fig.4 のように cad で簡単な製図をしたマスターを桁にぐるっと一周させて、それに合わせ るように円盤を桁に対して斜めに取り付けます。しっかりと桁にフィットしたことを確認

したら五分エポで仮固定しましょう。（この図で注意してほしいのは円盤は桁の端から順に 取り付けていきます！！いい写真がなかったので仕方なく妥協しました）このときしっか り五分エポが硬化するまで待つ、これがポイントです。早まる気持ちはわかります。誰だ って早く豪麺を食らいたいのですから。ただ 18 時からなのでそれだけは気を付けましょう。 その後は Fig.2 のように円盤→台形板→台形板→円盤→台形板→台形板→円盤の順に仮固 定し最後に 50 エポを桁と積層板の接着点に塗っていきましょう。硬化後、外筒に入るまで 積層板を削り微調整します。微調整の際は荒目の紙やすりを使ったほうが良いです。

- ウレタン発砲

50 エポでの固定が完了したらウレタンを発砲させましょう。適当な寸法の容器を用意し てその中でウレタンを発砲させます。注意点としては主剤と硬化剤をしっかりかき混ぜる、 これに尽きます。硬化剤の方が比重が重く下に溜まりやすいので下から上に持ち上げるよ うな感覚で 30 秒はかき混ぜましょう。それ以降は発砲してくるので早めに流し込みましょ う。ウレタンに関しては試作の際に实際にどのくらいで硬化するかなど体感しておくとい いと思います。とにかく焦らない、ギリギリまでかき混ぜる。あと使うウレタンに関して はなるべく発砲率の低いものを利用しました。これは単純に強度が高いためです。今年使 ったのは発砲率 7 倍とかその程度だったと記憶してます。ウレタンが硬化したら容器を破 壊して積層板を目安にヤスリでひたすらガリガリ削ります。

- 仕上げ


Fig.5 挿入シーン

どろどろのあたかい液体（エロジール＋タルク＋エポ）を万遍なく塗りたくり、外筒に 挿入し完成です。勿論ですが、罫書き線に合わせるのだけはお忘れなく。

## 5.最後に

皆さん、マルコミュ二ティという言葉ご存じですか？google でこの言葉を検索

にかけると「作業後に豪麺マルコに皆で行くことによって生まれる連帯感で満ち溢れた共 同体」と出てきます。鳥科内でよりこの考えが普遍的なものとなったら僕は泣いて喜びま す。今回は上反角のことについて簡単にまとめましたが、田中氏と一緒にフランジ・T 字な どの話題も加え、近い内に更新したいと思います。それでは、See you next time!


## 6.こんにちは T 字です

最後と言いましたが、2016 年パイロットの倉上君に「T 字についても・・・」と悲しそ うな顔で言われたので T 字の製作についても簡単にまとめておきます。

1) δ板について δ板は T 字のフィレット部につける直角二等辺三角形のカーボン製の板です。この人のお かげでオーバーレイの際カーボンが巻きやすくなったり、胴体桁が主翼桁に対して垂直に 接合されていることを保証してくれたりもします。（下の Fig.6 は T 字の概略図です、赤文 字が例のδ板です）


Fig.6 T 字概略図
δ板の大きさについては、コクピットフレームとの兼ね合いになるのでコクピ班とある 程度連携を取りながら寸法を決める必要がありますが、極端にδ板が小さいとオーバレ イの際巻きにくいのとパイロットの精神衛生上の問題上もあるので適度な妥協点を見 つけましょう。2015 年のδ板は積層枚数は確か 11 枚とかなり豪華でした。
2) 胴体桁の切断加工

さて、次は胴体の切断です。勿論グラインダーを使って処理しますが切断曲線がわからな い限りは何もできないのでマスターを作ります。ここで過去の偉人の出番となります。鳥 科に古から引き継がれている「胴体 接合 作成」という excel ファイルを使います。この え excel シートに胴体・主翼桁の桁径データを入力し（Fig.7）、そのプロットデータを cad に読み込ませてスプライン曲線を描きます。（Fig.8）


Fig.8 「胴体 接合 作成」

Fig.9 スプライン曲線

スプラインのボタンを押し、下のコマンド入力の部分に、さっきのエクセルのプロットの データを貼り付けます。そして。Enter キーを３回押し拡大するとこのようになります。印

刷したマスターを胴体桁に貼り付け、グラインダーでカットします。カットするという感 覚よりはディスク麺で削るという感覚の方が正しいかもしれません。

3) 胴体と 0 番の接着

胴体を加工した後に、胴体の先端にウレタンを流し込んで発砲させ、0 番との接着面積を 稼ぎます。そこにエポキシを塗り固定します。（Fig.10）


Fig.10 胴体 0 番接着の様子

作業を行うときは専用の治具を作成し、0 番を地面に水平になるようにしましょう。後は垂 直なレーザーを当て胴体の罫書き線に合わせながら固定します。（罫書き線は胴体には 90 度間隔で 4 本、0 番には前縁後縁側に二本引いておきましょう。）また、接着の際は 0 番の 後縁側と胴体桁の罫書き線がしっかりあっていることも同時に気を付ける必要があります。 ここをミスると翼の迎角がおかしくなってしまいます。


Fig.12 δ板の接着

δ板は罫書き線に合わせて接着していきます。このとき、上反角の時と同様にエロジール などの粘性を高めるものも混ぜておきましょう。このままだとオーバーレイしづらいので

パテ（紙粘土など）で適当な形にフィレットをつけるのも忘れずに。

4) オーバーレイ

オーバーレイとは T 字の 0 番と胴体桁の接着部にカーボンクロスを巻き、真空引きする工 程を指します。今年はカーボンを 11 枚巻きましたが、恐らく十分だと思います・・・カー ボンクロスを巻く際は下準備が大切で接合部に巻きやすいように予め切れ目をいれておく と非常にやりやすいと思います。(Fig.13)


Fig.13 カーボンクロスの切り込み例

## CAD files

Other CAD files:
【製作編】/CAD/竜海_ピトー管_固定具治具.dwg
【製作編】/CAD/フランジ治具マスター.dwg
【製作編】/CAD/竜海_本番機_垂直中子図面.dwg
【製作編】/CAD/【参考】Ray_水平機構.dwg
【製作編】/CAD/吊具_fromコクピ.dwg
【製作編】/CAD/水平部品_MDF成形マスター_5.5mm厚_ver.2.dwg
【製作編】/CAD/水平マウント治具_LC用_4mm厚_ver.2.dwg
【製作編】/CAD/垂直フランジ_接着and成形治具_ver.1.dwg
【製作編】/CAD/5.5mm_LC用_サーボホーン.dwg
【製作編】/CAD/竜海_本番機_T字CFカットマスター.dwg
【製作編】/CAD/竜海_本番機_水平機構.dwg

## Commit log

2025-04-15 Create 1. かんざし
2025-04-15 Update 1. かんざし
2025-04-15 Create 2. 木フラ
2025-04-15 Create 3. フランジ
2025-04-15 Update 2. 木フラ
2025-04-15 Create 4. T字
2025-04-15 Create 5. 吊り具
2025-04-15 Create 6. テール
2025-04-15 Create 7. 垂直尾翼
2025-04-15 Create 8. 水平尾翼
2025-04-15 Create 9. ピトー管
2025-04-15 Update and rename 製作編.md to 製作編 0. 目次.md
2025-04-15 Rename 製作編 0. 目次.md to 【製作編】 0. 目次.md
2025-04-15 Rename 【製作編】 0. 目次.md to 【製作編】0. 目次.md
2025-04-15 Rename 1. かんざし to 【製作編】1. かんざし
2025-04-15 Rename 2. 木フラ to 【製作編】2. 木フラ
2025-04-15 Rename 3. フランジ to 【製作編】3. フランジ
2025-04-15 Rename 4. T字 to 【製作編】4. T字
2025-04-15 Rename 5. 吊り具 to 【製作編】5. 吊り具
2025-04-15 Rename 6. テール to 【製作編】6. テール
2025-04-15 Rename 7. 垂直尾翼 to 【製作編】7. 垂直尾翼
2025-04-15 Rename 8. 水平尾翼 to 【製作編】8. 水平尾翼
2025-04-15 Rename 9. ピトー管 to 【製作編】9. ピトー管
2025-04-15 Update and rename 【製作編】1. かんざし to 【製作編】1. かんざし.md
2025-04-15 Rename 【製作編】2. 木フラ to 【製作編】2. 木フラ.md
2025-04-15 Rename 【製作編】3. フランジ to 【製作編】3. フランジmd
2025-04-15 Rename 【製作編】3. フランジmd to 【製作編】3. フランジ.md
2025-04-15 Rename 【製作編】4. T字 to 【製作編】4. T字.md
2025-04-15 Rename 【製作編】5. 吊り具 to 【製作編】5. 吊り具.md
2025-04-15 Rename 【製作編】6. テール to 【製作編】6. テール.md
2025-04-15 Rename 【製作編】7. 垂直尾翼 to 【製作編】7. 垂直尾翼.md
2025-04-15 Rename 【製作編】8. 水平尾翼 to 【製作編】8. 水平尾翼.md
2025-04-15 Rename 【製作編】9. ピトー管 to 【製作編】9. ピトー管.md
2025-04-15 Rename 【製作編】0. 目次.md to 【製作編】0. 初めに.md
2025-04-15 Update 【製作編】3. フランジ.md
2025-04-15 Update 【製作編】1. かんざし.md
2025-04-15 Update 【製作編】2. 木フラ.md
2025-04-15 Update 【製作編】4. T字.md
2025-04-15 Update 【製作編】5. 吊り具.md
2025-04-15 Update 【製作編】6. テール.md
2025-04-15 Update 【製作編】7. 垂直尾翼.md
2025-04-15 Update 【製作編】8. 水平尾翼.md
2025-04-15 Update 【製作編】0. 初めに.md
2025-04-21 Update 【製作編】9. ピトー管.md
2025-06-02 Rename 【製作編】0. 初めに.md to 【製作編】0. このサイトの使い方.md
2025-07-02 Update 【製作編】0. このサイトの使い方.md
2025-07-28 Create 購入リスト
2025-07-28 Update 購入リスト
2025-10-16 Create 【製作編】10. 上反桁カット
2025-10-16 Rename 【製作編】0. このサイトの使い方.md to 0. このサイトの使い方.md
2025-10-16 Rename 【製作編】1. かんざし.md to 1. かんざし.md
2025-10-16 Rename 【製作編】2. 木フラ.md to 2. 木フラ.md
2025-10-16 Rename 【製作編】3. フランジ.md to 3. フランジ.md
2025-10-16 Rename 【製作編】4. T字.md to 4. T字.md
2025-10-16 Rename 【製作編】5. 吊り具.md to 5. 吊り具.md
2025-10-16 Rename 【製作編】6. テール.md to 6. テール.md
2025-10-16 Rename 【製作編】7. 垂直尾翼.md to 7. 垂直尾翼.md
2025-10-16 Rename 【製作編】10. 上反桁カット to 10. 上反桁カット
2025-10-16 Rename 【製作編】8. 水平尾翼.md to 8. 水平尾翼.md
2025-10-16 Rename 【製作編】9. ピトー管.md to 9. ピトー管.md
2025-10-16 Rename 10. 上反桁カット to 【番外編】 上反桁カット
2025-10-16 Update 7. 垂直尾翼.md
2025-10-17 Update 8. 水平尾翼.md
2025-10-17 Update and rename 【番外編】 上反桁カット to 【番外編1】 上反桁カット
2025-10-17 Update 【番外編1】 上反桁カット
2025-10-17 Update and rename 【番外編1】 上反桁カット to 【番外編1】 上反桁カット.md
2025-10-17 Update 【番外編1】 上反桁カット.md
2025-10-18 Update and rename 【番外編】購入リスト to 【番外編】購入リスト.md
